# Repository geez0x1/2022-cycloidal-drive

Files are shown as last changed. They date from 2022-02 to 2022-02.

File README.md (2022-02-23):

This repository contains Python code and CAD files to (re)create the cycloidal gearing design, and experiments, from our paper _"3D-printable low-reduction cycloidal gearing for robotics"_.

Contents:

- Python code to aid in choosing and visualising design parameters
- CAD files of the presented prototype
- Python code for validation and testing using an ODrive motor controller

Everything is under the MIT license, so feel free to copy and modify as you see fit.

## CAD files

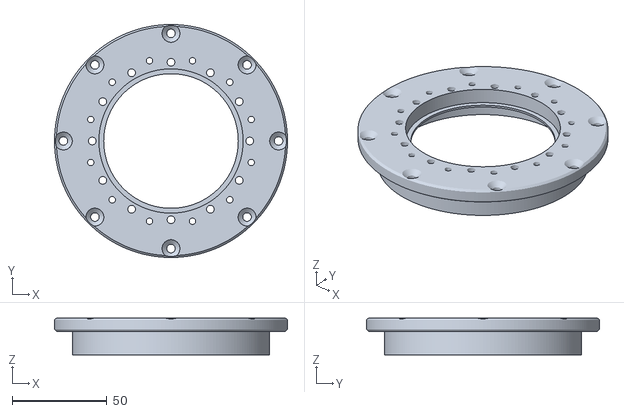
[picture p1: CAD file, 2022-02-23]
mechanical_design/Cycloidal drive main assembly/Cycloidal gearbox/Roller assembly/Gearbox housing top assembly/Gearbox housing top assembly v70.stl
122.8 x 122.8 x 19.5

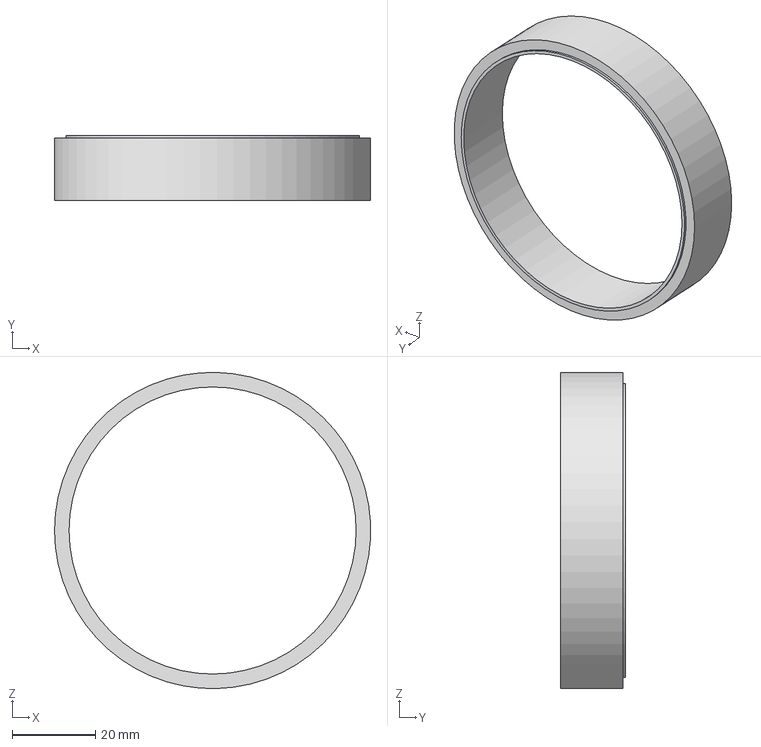
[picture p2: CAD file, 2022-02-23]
mechanical_design/Assembly tools/Bearing support v6.step
75.8 x 15.6 x 75.9 mm

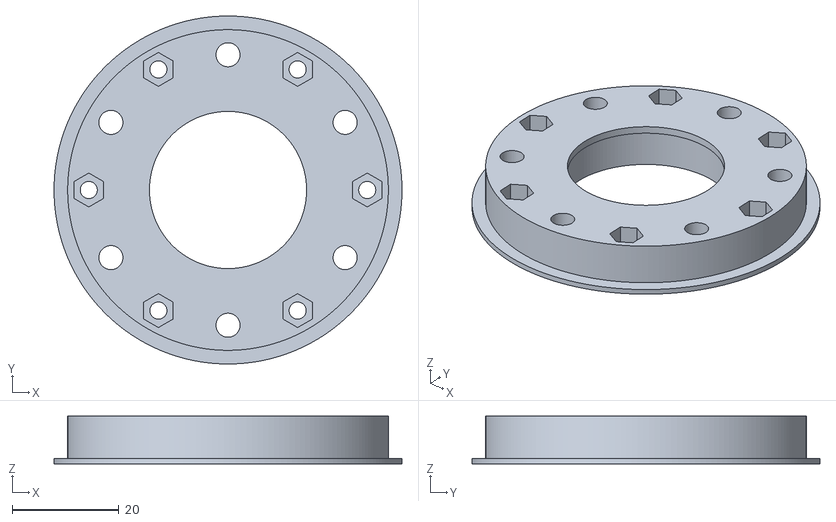
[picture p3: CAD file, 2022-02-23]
mechanical_design/Cycloidal drive main assembly/Cycloidal gearbox/Eccentric shaft assembly/Input shaft assembly/Output shaft v91.stl
65.1 x 65.1 x 8.90

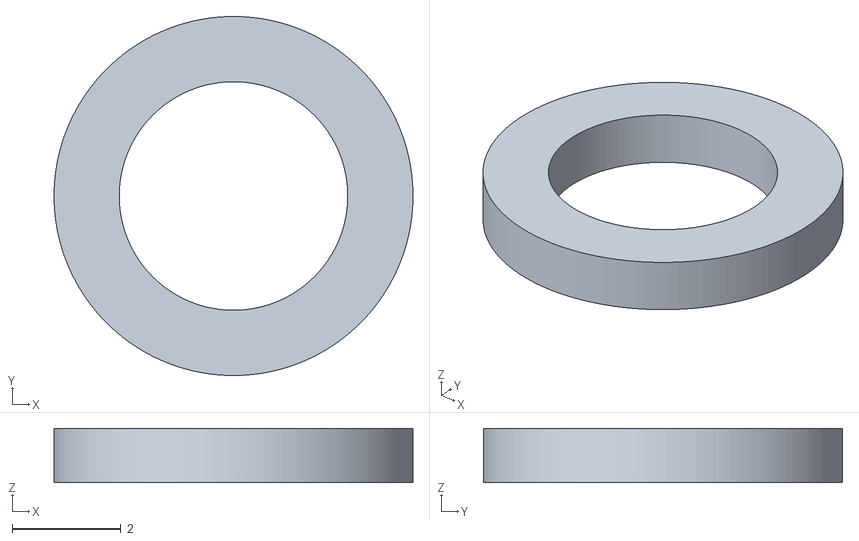
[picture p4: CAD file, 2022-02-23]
mechanical_design/Cycloidal drive main assembly/Cycloidal gearbox/Eccentric shaft assembly/Output shaft stiffness ring assembly/Bearing spacer v6.stl
6.60 x 6.60 x 1.00

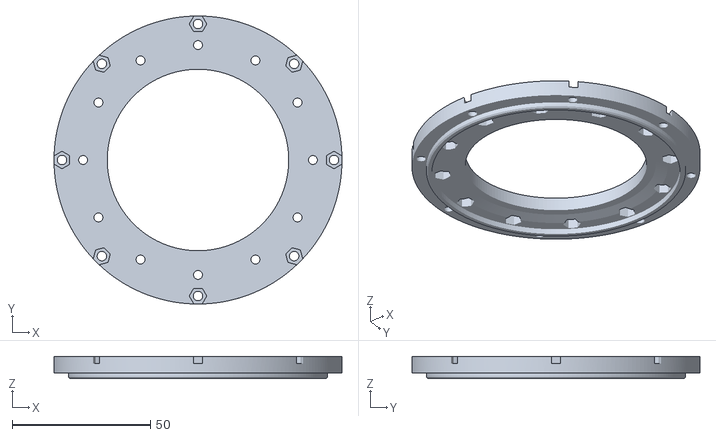
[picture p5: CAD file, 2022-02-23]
mechanical_design/Cycloidal drive main assembly/Cycloidal gearbox/Gearbox housing bottom v120.stl
104.0 x 104.0 x 8.00

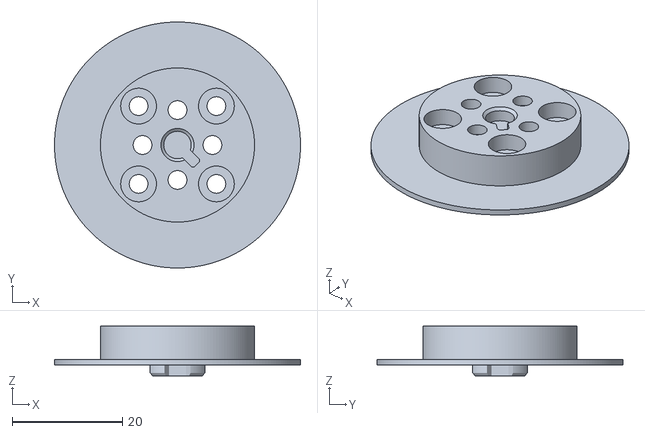
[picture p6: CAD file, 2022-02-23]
mechanical_design/Cycloidal drive main assembly/Motor housing assembly/Motor assembly/Motor shaft v63.stl
44.7 x 44.7 x 9.00

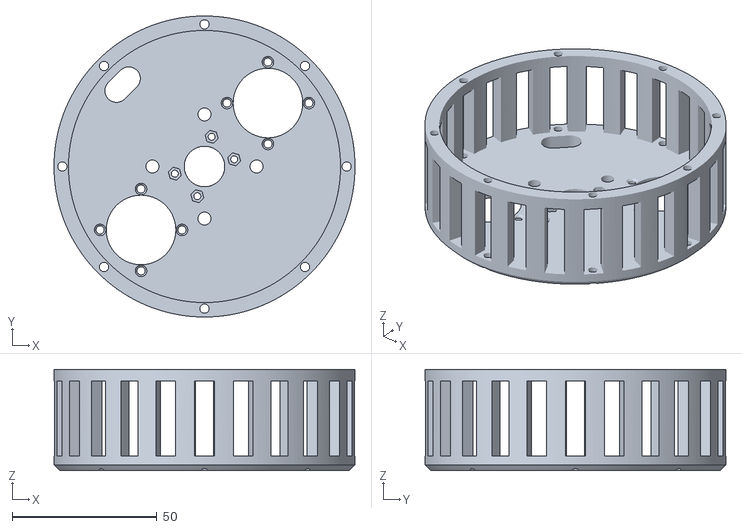
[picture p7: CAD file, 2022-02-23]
mechanical_design/Cycloidal drive main assembly/Motor housing assembly/Motor housing v122.stl
104.0 x 104.0 x 35.0

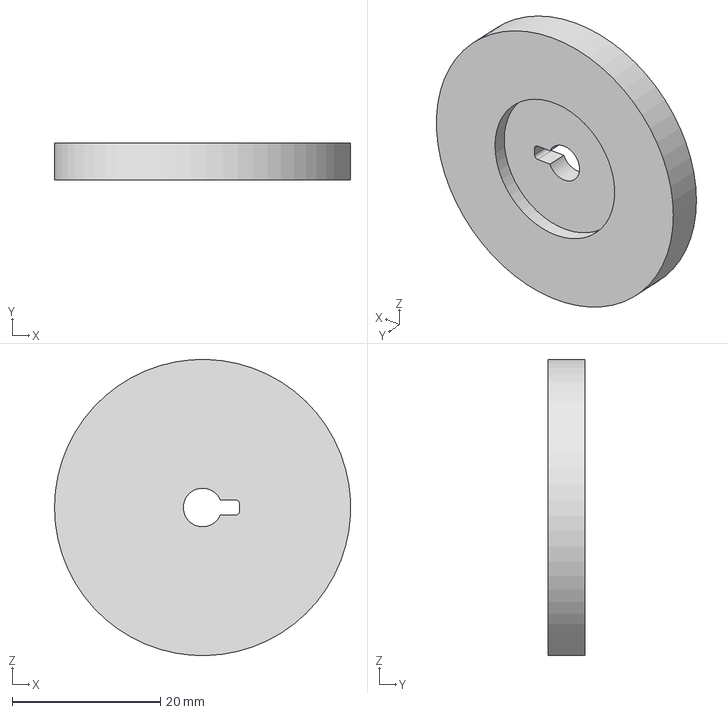
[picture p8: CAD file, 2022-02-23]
mechanical_design/Assembly tools/Input shaft base v7.step
40.0 x 5.00 x 40.0 mm

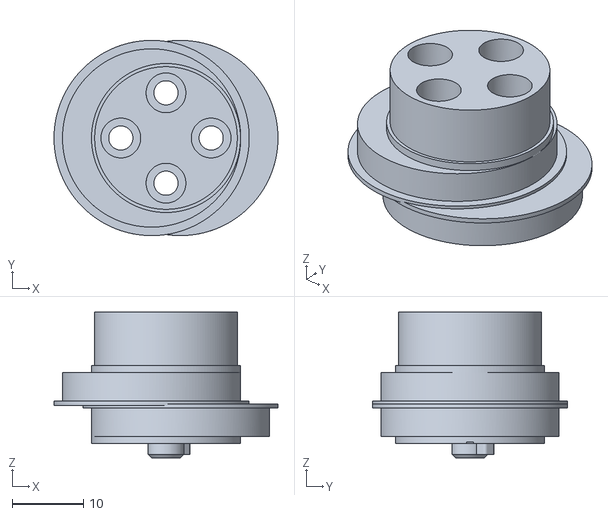
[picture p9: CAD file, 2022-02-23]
mechanical_design/Cycloidal drive main assembly/Cycloidal gearbox/Eccentric shaft assembly/Input shaft assembly/Input shaft v70.stl
31.5 x 27.4 x 20.5

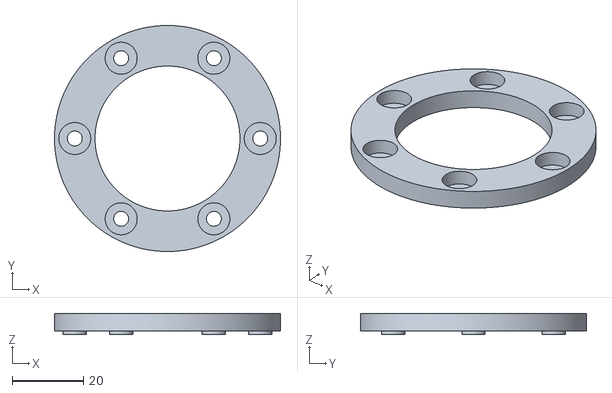
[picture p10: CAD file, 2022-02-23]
mechanical_design/Cycloidal drive main assembly/Cycloidal gearbox/Eccentric shaft assembly/Output shaft stiffness ring assembly/Output shaft stiffness ring v37.stl
63.5 x 63.5 x 6.00

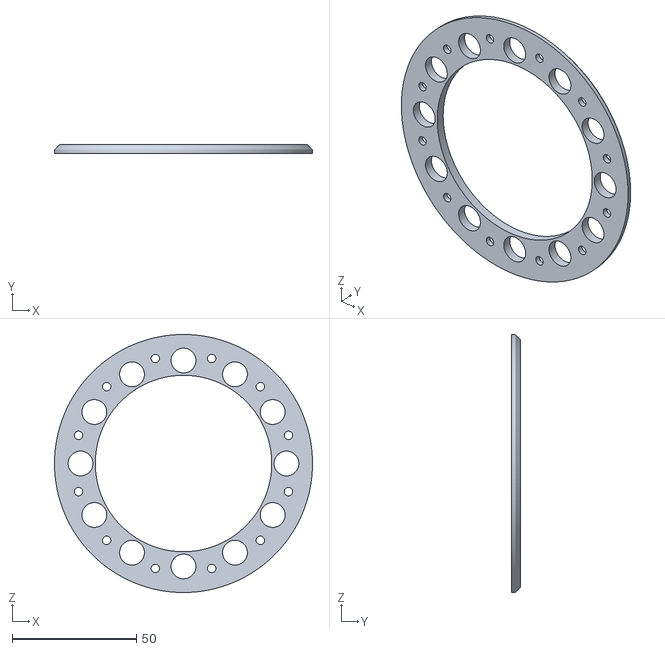
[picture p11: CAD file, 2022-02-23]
mechanical_design/Cycloidal drive main assembly/Cycloidal gearbox/Roller assembly/Gearbox housing top assembly/Output bearing retaining bracket v12.stl
104.0 x 3.50 x 104.0

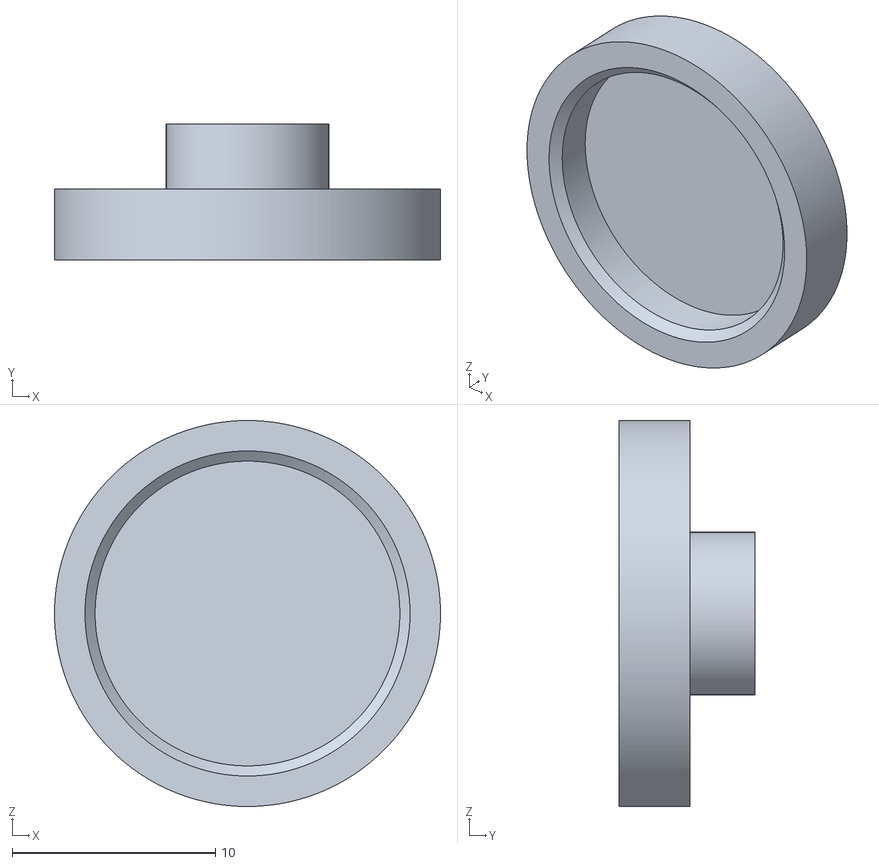
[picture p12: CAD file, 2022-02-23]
mechanical_design/Cycloidal drive main assembly/Motor housing assembly/Motor assembly/Magnet holder v8.stl
19.0 x 6.70 x 19.0

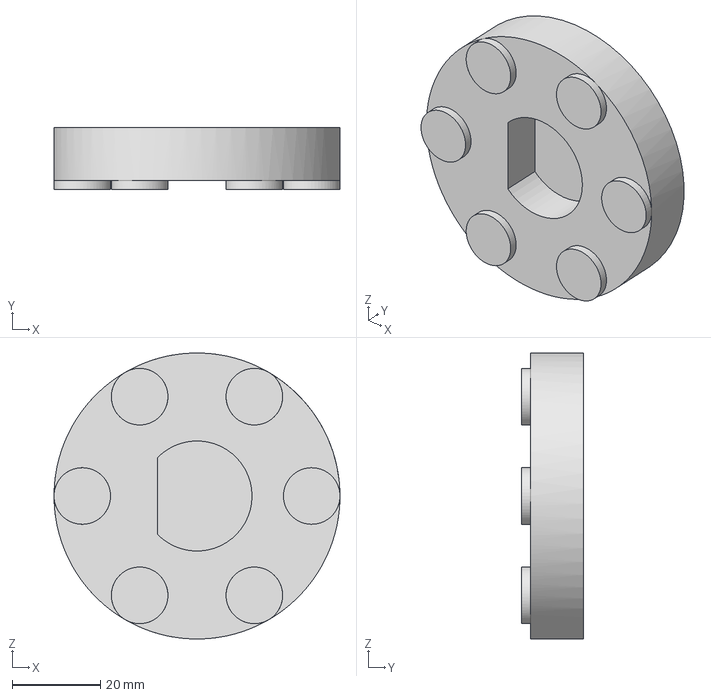
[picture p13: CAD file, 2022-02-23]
mechanical_design/Assembly tools/Rotor press v8.step
65.0 x 14.0 x 65.0 mm

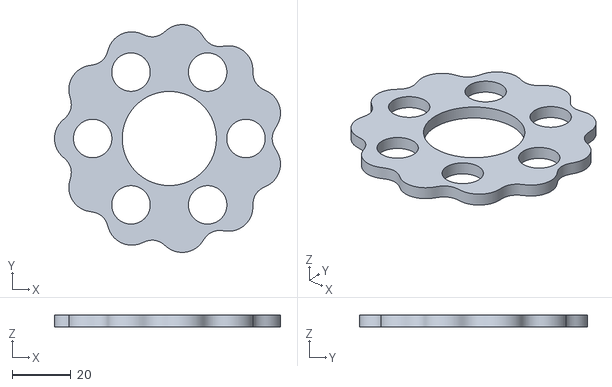
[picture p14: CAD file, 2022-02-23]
mechanical_design/Cycloidal drive main assembly/Cycloidal gearbox/Eccentric shaft assembly/Input shaft assembly/Rotor (R = 4.15 - N = 12 - Rr = 0.45) v25.stl
76.8 x 77.4 x 4.00

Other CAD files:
mechanical_design/Assembly tools/Bearing support v6.stl
mechanical_design/Assembly tools/Input shaft base v7.stl
mechanical_design/Assembly tools/Rotor press v8.stl

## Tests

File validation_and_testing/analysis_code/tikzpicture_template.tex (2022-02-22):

\begin{tikzpicture}
	\begin{axis}[
		width=0.87\linewidth, % Approximately full line width
		height=0.87\linewidth/1.61, % Golden ratio
		scale only axis,
		%title={My fancy plot of {$filename}},
		%title style={at={(0.5,0.95)}},
		xlabel={$$x$$},
		ylabel={$$y$$},
		legend entries={},
		%xtick distance=1,
		%ytick distance=1,
		grid=major,
		grid style={gray!25},
		%ymin=0,
		%ymax=1,
		enlarge x limits = false,
		%enlarge y limits = 0.05, % To reduce y-axis margins
		title style={font=\small},
		legend style={
			font=\footnotesize,
			%at={(0.5,0.5)}, % To reposition legend
			%legend pos = south west, % To reposition legend
			cells={anchor=west},
		},
		label style={font=\small},
		tick label style={font=\footnotesize},
		xlabel shift={-2},
		ylabel shift={-5},
		line width = 0.6pt,
		%clip mode=individual, % Force the marks to be behind lines
	]
		%\addplot[blue] table[x=x, y=y, col sep=comma] {$filename};
		%\addplot[red] table[x=x, y=y2, col sep=comma] {$filename};
	\end{axis}
\end{tikzpicture}%

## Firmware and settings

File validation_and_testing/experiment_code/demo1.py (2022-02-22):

#!/usr/bin/env python3
# -*- coding: utf-8 -*-
"""
Created on Fri Nov 26 11:14:38 2021

@author: wesley
"""

from __future__ import print_function

import odrive
from odrive.enums import *
import time
import math
import csv
from common import get_output_filename, save_data

# Experiment parameters (pendulum)
def loadInertia():
	m_weights	= 2.0		# Weight plates mass [kg]
	m_bar		= 0.432		# Pendulum mass [kg]
	m_mounting	= 0.211		# Mounting stuff (thread, nuts, etc) [kg]
	L			= 0.5		# Pendulum length

	return (m_weights+m_mounting) * L**2 + (1/3) * m_bar * L**2

# Experiment parameters (LIGHT SHORT pendulum)
def loadInertia_light():
	m_weights	= 0.0		# Weight plates mass [kg]
	m_bar		= (44/50)*0.432 # Pendulum mass [kg]
	m_mounting	= 0			# Mounting stuff (thread, nuts, etc) [kg]
	L			= 0.44		# Pendulum length

	return (m_weights+m_mounting) * L**2 + (1/3) * m_bar * L**2


# Demo parameters
sample_time		= 0.0125	# Sample time [s] # Limited by USB/UART?
n				= 11	# True gear ratio
turns2deg		= 360	# One turn in [deg]
deg2rad			= math.pi/180 # Degrees to radians
turns2rad		= turns2deg*deg2rad # Turns to rad []
inertia			= 0.0*loadInertia()	# Load inertia

# Motion behaviour
max_speed		= 10	# Max output speed [rad/s]
max_accel		= 10	# Max acceleration/deceleration [rad/s^2]
target_pos		= [math.pi, 1.5*math.pi, 0.5*math.pi, 2*math.pi] # Target positions [rad]
static_time		= 0.05	# How long to stand still between positions [s]
reached_margin	= 0.01	# Acceptable error for reaching setpoint [rad], at output

# Control gains
pos_gain			= 15*20		# [turns/s / turn] - default 20
vel_gain			= 20*0.16	# [Nm / turns/s] - default 0.16
vel_integrator_gain	= 20*0.32	# [Nm / turn/s^2] - default 0.32
current_lim			= 60		# Current limit [A] (40A tops out at around 31 Nm)
requested_current	= 80		# Current sensing limit [A]
# Not touching current control gains current_gain and
# current_integrator_gain - they are automatically set
# for a given current control bandwidth.

# Prompt user for output filename
out_filename = get_output_filename('out_demo1.csv')

# Find a connected ODrive (this will block until you connect one)
print("Finding odrive..")
my_drive = odrive.find_any()

# First set the reference position to whatever the current position is
input_pos_initial = my_drive.axis0.encoder.pos_estimate
my_drive.axis0.controller.input_pos = input_pos_initial
print('Initial position offset is', round(turns2rad*input_pos_initial/n,2), 'rad.')
print('NOTE: Make sure to start this experiment in a down hanging position!')

# Set control mode
# "Trajectory control" - essentially minimum jerk
print('Setting control mode and parameters..')
my_drive.axis0.controller.config.control_mode	= CONTROL_MODE_POSITION_CONTROL
my_drive.axis0.controller.config.input_mode		= INPUT_MODE_TRAP_TRAJ
my_drive.axis0.trap_traj.config.vel_limit		= n * max_speed / turns2rad
my_drive.axis0.trap_traj.config.accel_limit		= n * max_accel / turns2rad
my_drive.axis0.trap_traj.config.decel_limit		= n * max_accel / turns2rad
my_drive.axis0.controller.config.inertia		= inertia

# Set control gains
my_drive.axis0.controller.config.pos_gain = pos_gain
my_drive.axis0.controller.config.vel_gain = vel_gain
my_drive.axis0.controller.config.vel_integrator_gain = vel_integrator_gain

# Set current limit
my_drive.axis0.motor.config.current_lim = current_lim
my_drive.axis0.motor.config.requested_current_range = requested_current

print('Starting closed loop control..')
my_drive.axis0.requested_state = AXIS_STATE_CLOSED_LOOP_CONTROL
time.sleep(1.0)

# Record data
print('Recording data..')
data = []
t0 = time.monotonic()

# Iterator through target positions
motion_it = 0
motion_setpoint_reached = True
t_motion_setpoint_reached = t0

# Until we break..
while True:
	# Get iteration start time
	t = time.monotonic()

	# Get data
	motorPos    = my_drive.axis0.encoder.pos_estimate
	outputPos   = 0#my_drive.axis1.encoder.pos_estimate # Encoder not available, and not really needed
	motorVel    = my_drive.axis0.encoder.vel_estimate
	outputVel   = 0#my_drive.axis1.encoder.vel_estimate # Encoder not available, and not really needed
	Iq_set		= my_drive.axis0.motor.current_control.Iq_setpoint
	Iq_meas		= my_drive.axis0.motor.current_control.Iq_measured
	data.append([
		t-t0,
		motorPos,
		outputPos,
		motorVel,
		outputVel,
		my_drive.axis0.controller.input_pos,
		Iq_set,
		Iq_meas,
	])

	# Check if we have reached the setpoint
	# Compute error in [rad], at the output
	if not motion_setpoint_reached:
		e = turns2rad * (my_drive.axis0.controller.input_pos - motorPos) / n
		if math.fabs(e) <= reached_margin:
			t_motion_setpoint_reached = time.monotonic()
			motion_setpoint_reached = True # Don't keep updating the reached time
			print('Setpoint reached.')

	# If there has been more time than `static_time` since we reached the setpoint, let's go
	if motion_setpoint_reached and time.monotonic() - t_motion_setpoint_reached >= static_time:
		# Check whether we have reached all set points, and then the starting position
		if motion_it >= len(target_pos)+1:
			# If we have reached the starting position, we can stop
			break
		elif motion_it >= len(target_pos):
			# If we have reached all target positions, we go to the starting position
			target_pos_motor = input_pos_initial
		else:
			# Otherwise we go to the next target position
			target_pos_motor = input_pos_initial + n * target_pos[motion_it] / turns2rad # Motor pos in [turns]

		print('Updating set point to', round(target_pos_motor*turns2rad/n,2), 'rad..')

		# Set new set point
		my_drive.axis0.controller.input_pos = target_pos_motor

		# Update iterator for setpoints so we set the next one next time
		motion_it += 1

		# We have not reached the new setpoint yet
		motion_setpoint_reached = False

	# Sleep for loop
	try:
		time.sleep(sample_time - (time.monotonic()-t))
	except:
		print('    WARNING: Iteration took longer than sample time of', sample_time, 's')

# Stop motor
# TODO CAN WE REMOVE THIS?
print('Finished, again setting initial position (should be no move, in which case remove this)..')
my_drive.axis0.controller.input_pos = input_pos_initial
time.sleep(1)

# Stop controller
print('Stopping closed-loop control..')
my_drive.axis0.requested_state = AXIS_STATE_IDLE

# Save data
save_data(data, out_filename)

# End
print('Done.')

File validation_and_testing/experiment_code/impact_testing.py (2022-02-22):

#!/usr/bin/env python3
# -*- coding: utf-8 -*-
"""
Created on Fri Nov 26 11:14:38 2021

@author: wesley
"""

from __future__ import print_function

import odrive
from odrive.enums import *
import time
import math
import csv
import curses
from common import get_output_filename, save_data, append_filename

def main(stdscr):
	# Test parameters
	sample_time		= 0.01	# Sample time [s] # Limited by USB/UART?
	n				= 11	# Gear ratio []
	deg_per_step	= 90	# Degrees to increment per step (on the output)
	turns2deg		= 360	# One turn in degrees []
	deg2rad			= math.pi/180 # Degrees to radians []
	turns2rad		= turns2deg*deg2rad # Turns to rad []

	# Control gains
	# Increase the following control gains as appropriate to get
	# very stiff position control for this test.
	pos_gain		= 5*20		# [turns/s / turn] - default 20
	vel_gain		= 5*0.16	# [Nm / turns/s] - default 0.16
	vel_integrator_gain = 5*0.32	# [Nm / turn/s^2] - default 0.32
	current_lim			= 60		# Current limit [A] (40A tops out at around 31 Nm)
	requested_current	= 80		# Current sensing limit [A]
	# Not touching current control gains current_gain and
	# current_integrator_gain - they are automatically set
	# for a given current control bandwidth.

	# Prompt user for output filename
	out_filename = get_output_filename('out_impact_testing.csv', stdscr)
	out_filename_stiffness = append_filename(out_filename, '_stiffness')

	# curses: disable echo
	curses.noecho()
	# curses: make getch() non-blocking
	stdscr.nodelay(1)
	line = 0

	# Find a connected ODrive (this will block until you connect one)
	stdscr.addstr(line,0,'Finding odrive..'); line += 1
	my_drive = odrive.find_any()

	# First set the reference position to whatever the current position is
	input_pos = my_drive.axis0.encoder.pos_estimate
	my_drive.axis0.controller.input_pos = input_pos
	input_pos_initial = input_pos
	stdscr.addstr(line,0,'Initial position offset is '+str(round(turns2deg*input_pos_initial/n,2))+' deg.'); line += 1

	# Set control mode
	# Position control
	stdscr.addstr(line,0,'Setting control mode and parameters..'); line += 1
	my_drive.axis0.controller.config.control_mode = CONTROL_MODE_POSITION_CONTROL
	my_drive.axis0.controller.config.input_mode = INPUT_MODE_POS_FILTER
	my_drive.axis0.controller.config.input_filter_bandwidth = 5.0 # [Hz]

	# Set control gains
	my_drive.axis0.controller.config.pos_gain = pos_gain
	my_drive.axis0.controller.config.vel_gain = vel_gain
	my_drive.axis0.controller.config.vel_integrator_gain = vel_integrator_gain
	
	# Set current limit
	my_drive.axis0.motor.config.current_lim = current_lim
	my_drive.axis0.motor.config.requested_current_range = requested_current

	# Compute turns to increment per step [] (on the output)
	turns_per_step	= deg_per_step/turns2deg

	# Then start position control
	stdscr.addstr(line,0,'Starting closed loop control..'); line += 1
	my_drive.axis0.requested_state = AXIS_STATE_CLOSED_LOOP_CONTROL
	time.sleep(1.0)

	# Record data
	stdscr.addstr(line,0,'Recording data..'); line += 1
	data = []
	data_stiffness = []
	t0 = time.monotonic()

	# Loop until told to stop
	line += 1; stdscr.addstr(line,0,'Use +/- to increase/decrease position, or press \'q\' to stop.'); line += 1; line += 1
	outputPos_deg = round(turns2deg*(input_pos-input_pos_initial)/n,2)
	stdscr.addstr(line,4,'Current output position: '+str(outputPos_deg)+' deg..')
	while True:
		# Get iteration start time
		t = time.monotonic()
		
		# curses: get keyboard input, returns -1 if none available
		c = stdscr.getch()

		if c == ord('+') or c == ord('='):
			input_pos += turns_per_step * n
			my_drive.axis0.controller.input_pos = input_pos

			outputPos_deg = round(turns2deg*(input_pos-input_pos_initial)/n,2)
			stdscr.addstr(line,4,'Current output position: '+str(outputPos_deg)+' deg..')

		elif c == ord('-'):
			input_pos -= turns_per_step * n
			my_drive.axis0.controller.input_pos = input_pos

			outputPos_deg = round(turns2deg*(input_pos-input_pos_initial)/n,2)
			stdscr.addstr(line,4,'Current output position: '+str(outputPos_deg)+' deg..')

		elif c == ord('q'):
			line += 1
			break

		# Get data
		motorPos    = my_drive.axis0.encoder.pos_estimate
		outputPos   = 0#my_drive.axis1.encoder.pos_estimate
		motorVel    = my_drive.axis0.encoder.vel_estimate
		outputVel   = 0#my_drive.axis1.encoder.vel_estimate
		Iq_set		= my_drive.axis0.motor.current_control.Iq_setpoint
		Iq_meas		= my_drive.axis0.motor.current_control.Iq_measured
		data.append([
			t-t0,
			motorPos,
			outputPos,
			motorVel,
			outputVel,
			input_pos,
			Iq_set,
			Iq_meas,
		])
		
		# Sleep for loop
		try:
			time.sleep(sample_time - (time.monotonic()-t))
		except:
			print('    WARNING: Iteration took longer than sample time of', sample_time, 's')

	# Stop controller
	line += 1; stdscr.addstr(line,0,'Finished, stopping closed-loop control..'); line += 1
	my_drive.axis0.requested_state = AXIS_STATE_IDLE
	c = stdscr.getch()
	time.sleep(1)

	# Stop curses window
	curses.endwin()

	# Save data
	save_data(data, out_filename)

	# End
	print('Done.')


# Run
if __name__ == '__main__':
	curses.wrapper(main)

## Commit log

2022-02-23 Adding cycloidal drive CAD
    [Bearing spacer v6.stl, Gearbox housing bottom v120.stl, Gearbox housing top assembly v70.stl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]
2022-02-23 Adding assembly tools
    [Bearing support v6.step, Bearing support v6.stl, Input shaft base v7.step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]
